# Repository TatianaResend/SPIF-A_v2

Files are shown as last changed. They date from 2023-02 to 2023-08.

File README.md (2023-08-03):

<!-- Improved compatibility of back to top link: See: https://github.com/othneildrew/Best-README-Template/pull/73 -->

<!--
*** Thanks for checking out the Best-README-Template. If you have a suggestion
*** that would make this better, please fork the repo and create a pull request
*** or simply open an issue with the tag "enhancement".
*** Don't forget to give the project a star!
*** Thanks again! Now go create something AMAZING! :D
-->

<!-- PROJECT SHIELDS -->
<!--
*** I'm using markdown "reference style" links for readability.
*** Reference links are enclosed in brackets [ ] instead of parentheses ( ).
*** See the bottom of this document for the declaration of the reference variables
*** for contributors-url, forks-url, etc. This is an optional, concise syntax you may use.
*** https://www.markdownguide.org/basic-syntax/#reference-style-links
-->
[][contributors-url]
[][forks-url]
[][stars-url]
[][issues-url]
[][license-url]

<!-- PROJECT LOGO -->
<br />
<div align="center">
  <a href="https://github.com/othneildrew/Best-README-Template">
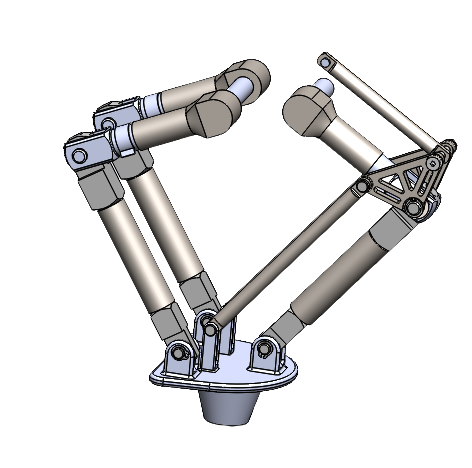
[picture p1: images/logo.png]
    
  </a>

  <h3 align="center">SPIF-A_v2</h3>

  <p align="center">
  It consists of the development of an incremental stamping machine   
  <br />
    <a href="https://github.com/TatianaResend/SPIFA-e-v2.0"><strong>Explore the docs »</strong></a>
    <br />
    <br />
    <a href="https://github.com/TatianaResend/SPIFA-e-v2.0/blob/main/README.md">View Demo</a>
    ·
    <a href="https://github.com/TatianaResend/SPIFA-e-v2.0/issues">Report Bug</a>
    ·
    <a href="https://github.com/TatianaResend/SPIFA-e-v2.0/issues">Request Feature</a>
  </p>
</div>

<!-- TABLE OF CONTENTS -->
<details>
  <summary>Table of Contents</summary>
  <ol>
    <li><a href="#about-the-project">About The Project</a></li>
    <li><a href="#machine-structure-design">Machine structure design</a>
      <ul>
        <li><a href="#base-requirements">Base requirements</a></li>
        <li><a href="#architecture">Architecture</a></li>
        <li><a href="#direct-and-indirect-kinematic-analysis">Direct and indirect kinematic analysis</a></li>
      </ul>
    </li>
    <li><a href="#mechanical-project">Mechanical project</a></li>
    <li><a href="#automation-project">Automation project</a></li>
    <li><a href="#contributing">Contributing</a></li>
    <li><a href="#license">License</a></li>
    <li><a href="#contact">Contact</a></li>
  </ol>
</details>

<!-- ABOUT THE PROJECT -->
# About The Project
The project serves as the focal point of the master's thesis in mechanical engineering. The primary goal of this project is to develop a compact incremental forming machine. The machine will be electric, ensuring a silent operation and compact size to facilitate coexistence with 3D printers. To effectively cover all aspects of machine construction, the project has been divided into three key areas: machine structure design, mechanical project, and automation project.

<!-- GETTING STARTED -->
# Machine structure design

## Base requirements:

|  |  |
| --- | --- |
| Number of axels | 3 |
| Working area  | 200 x 200 mm  |
| Vertical stroke  | 100 mm  |
| Sheet thickness  | 0,5 to 3 mm |
| Sheet material | aluminum |
| Conformation forces | 3 kN (vert.) 1 kN (hor.) |
| Motors | Nema 34 |

## Architecture:

The study of possible configurations is demonstrated in issues [#1](/../../issues/1) to [#4](/../../issues/4). After the analysis it is concluded that the best configuration is case 1.1.1..
To choose the best configuration, the lowest possible torque was taken into account.

- 2 arms in parallel (delta 2)
- Distance between motors: 50 mm
- L1 = 120;
- L2 = 150;
- y _ work area = -320 mm
- Maximum torque: 665 Nm 

## Direct and indirect kinematic analysis:
The direct and indirect kinematics are represented in the issue [#16](/../../issues/16) and in chapter 3.3 of the [thesis](https://github.com/TatianaResend/SPIF-A_v2/blob/main/Master's%20thesis.pdf) document.


# Mechanical project
Mechanical projects steps:
- Arm design
- Support system for the forming punch
- Selection and sizing of the motor-reducer set
- Selection and sizing of the linear motor-autorator set
- Structural configuration







### Simulation:
Two types of simulations were carried out using Solidworks: **with motion analysis** and **static** . Both analyzes are described in section 4.6.1 and 4.6.2, respectively, in the [thesis](https://github.com/TatianaResend/SPIF-A_v2/blob/main/Master's%20thesis.pdf) document. Some steps for carrying out the simulations are described in the issue [#5](/../../issues/5).

# Automation project
Automation projects steps:
- Wiring Diagram and Main Components
- Power Circuit
- Controller (**Controllino MEGA**)
- Drive (**CL86T Closed-loop Stepper Drive**)
- Security Elements
- Switchboard
- Motion Control: Implementation of Kinematics, Determination of the Number of Pulses, Incremental Positioning
- Graphic User Interface: Manual Mode, Automatic Mode, Information Page

<p align="center">
  
</p>

All steps of the automation project as well as its implementation are described in chapters 5 and 6.2 of the [thesis](https://github.com/TatianaResend/SPIF-A_v2/blob/main/Master's%20thesis.pdf) document. It is also possible to find some information in the issues [#15](/../../issues/15), [#17](/../../issues/17) - [#20](/../../issues/20), [#22](/../../issues/22) e [#23](/../../issues/23). The developed code can be found [here](https://github.com/TatianaResend/SPIF-A_v2/tree/main/CODE). The controller program was carried out in the **Arduino IDE** platform and the code for the GUI in **MATLAB.**

<!-- CONTRIBUTING -->
# Contributing

If you have a suggestion that would make this better, please fork the repo and create a pull request. You can also simply open an issue with the tag "enhancement".
Don't forget to give the project a star! Thanks again!

1. Fork the Project
2. Create your Feature Branch (`git checkout -b feature/AmazingFeature`)
3. Commit your Changes (`git commit -m 'Add some AmazingFeature'`)
4. Push to the Branch (`git push origin feature/AmazingFeature`)
5. Open a Pull Request

<p align="right">(<a href="#readme-top">back to top</a>)</p>

<!-- LICENSE -->
# License

Distributed under the GPL License. See `LICENSE.txt` for more information.

<p align="right">(<a href="#readme-top">back to top</a>)</p>

<!-- CONTACT -->
# Contact

Tatiana Resende - tatianaresende@ua.pt

Project Link: [SPIF-A_v2](https://github.com/TatianaResend/SPIFA-e-v2.0)

 <!-- <p align="right">(<a href="#readme-top">back to top</a>)</p> -->

<!-- ACKNOWLEDGEMENTS -->
### Acknowledgements
- Professor Ricardo Sousa - rsousa@ua.pt
- Professor Daniel Afonso - dan@ua.pt

<p align="right">(<a href="#readme-top">back to top</a>)</p>

<!-- MARKDOWN LINKS & IMAGES -->
<!-- https://www.markdownguide.org/basic-syntax/#reference-style-links -->
[contributors-shield]: https://img.shields.io/github/contributors/TatianaResend/SPIF-A_v2.svg?style=for-the-badge
[contributors-url]: https://github.com/TatianaResend/SPIF-A_v2/contributors
[forks-shield]: https://img.shields.io/github/forks/TatianaResend/SPIF-A_v2.svg?style=for-the-badge
[forks-url]: https://github.com/TatianaResend/SPIF-A_v2/network/members
[stars-shield]: https://img.shields.io/github/stars/TatianaResend/SPIF-A_v2.svg?style=for-the-badge
[stars-url]: https://github.com/TatianaResend/SPIF-A_v2/stargazers
[issues-shield]: https://img.shields.io/github/issues/TatianaResend/SPIF-A_v2.svg?style=for-the-badge
[issues-url]: https://github.com/TatianaResend/SPIF-A_v2/issues
[license-shield]: https://img.shields.io/github/license/TatianaResend/SPIF-A_v2.svg?style=for-the-badge
[license-url]: https://github.com/TatianaResend/SPIF-A_v2/blob/master/LICENSE.txt

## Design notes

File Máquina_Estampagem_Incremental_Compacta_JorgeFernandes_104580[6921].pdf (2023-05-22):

# RELATÓRIO

# Projeto e controlo de uma máquina de estampagem incremental compacta

### Jorge Fernandes, nº 104580

Curso Mestrado em Engenharia e Automação Industrial Disciplina Projeto em Engenharia de Automação

Ano letivo 2020/2021

Data | 16/07/2021
Orientador Professor Doutor Daniel Gil Afonso

Resumo Projeto do quadro elétrico, seleção de motores e programação da cinemática de uma máquina compacta para estampagem incremental baseada num braço RR plano.

Índice remissivo

Índice de figuras

### 1. Introdução

A utilização de máquinas controlados por comandos numéricos tem vindo a aumentar nas últimas décadas. São exemplos disso, o uso de CNCs, máquinas de corte a laser, impressoras 3D, braços robotizados, etc. Todos estes equipamentos trazem benefícios para a indústria em geral, reduzindo tempos de fabrico de componentes e aumentando a repetibilidade.
Por norma, o seu acionamento é feito por meio de um código, interpretado pela máquina de forma sequencial, contendo um conjunto de posições e/ou ações a ser tomadas. Este código, designado de código máquina ou g-code, é interpretado por um controlador responsável por acionar os componentes da máquina, como por exemplo motores, termístores, fusos, entre outros.

Neste projeto pretende-se selecionar um conjunto de componentes para controlo de uma máquina de estampagem incremental compacta baseada num braço robótico RR plano. Esta máquina tem um total de 3 eixos, X, Y, Z e será controlada por um controlador a selecionar. O controlador será responsável pela cinemática da máquina, para que se consiga o correto posicionamento da ferramenta de estampagem, um punção, nas múltiplas posições desejados de modo a conformar a chapa com a forma pretendida.
No decorrer deste projeto são selecionados: motores, drivers e todos os componentes elétricos de funcionamento e segurança necessário para o quadro elétrico. É determinada a cinemática da máquina e implementado o código para interpretação de comandos numéricos vindos do computador por porta de comunicação. Por último é desenvolvido uma interface para computador, de modo que o utilizador possa controlar a máquina de forma prática.

### 1.1 Estampagem incremental

O processo de estampagem incremental consiste numa tecnologia utilizada para conformar chapas de metal utilizando deformações incrementais sequenciais. É utilizada uma ferramenta de ponta arredondada, acoplada a uma CNC ou braço robótico, que deforma a chapa com o contorno da peça pretendida.
O percurso de uma peça fabricada por estampagem incremental começa pelo desenhado num software de CAD que é depois transferido para uma CNC, com o correto prato e sistema de grampos ou gabarito. Posiciona-se a chapa de metal na posição desejada, alinhada com a ferramenta de deformação e dá-se início ao processo. Finalizada a deformação, a peça está pronta a utilizar, não necessitando de nenhum processo adicional.
As principais aplicações de peças conformadas por estampagem incremental são protótipos, aplicações na medicina, aplicações aeronáuticas e automotivas sendo as suas vantagens:
- Facilidade na prototipagem rápida;
- Forças de conformação baixas, devido à natureza do processo incremental;
- É facilmente adaptado a qualquer tipo de CNC;
- Peças finais são produzidas diretamente dos ficheiros CAD;
- Não necessita de matrizes adicionais para a conformação;
- As dimensões das peças só são limitadas pelas dimensões da máquina;
- Excelente acabamento superficial.
Por outro lado, as desvantagens deste processo são:
- Elevados tempos de conformação quando comparado com outros processos de estampagem;
- Apresenta menor precisão dimensional especialmente em zonas com ângulos acentuados;
- Dificuldades na obtenção de ângulos retos;
- Pode ocorrer retorno do material (springback) após a conformação.
A Figura 1 ilustra alguns exemplos de estampagem incremental:

Figura 1 - Estampagem incremental

### 1.2 Máquina de estampagem incremental compacta

O projeto de construção de uma máquina de estampagem incremental compacta parte da necessidade de utilização de peças estampadas para protótipos. O acesso a uma máquina deste tipo, em conjunto com o uso de fresadoras ou impressoras 3D facilita a prototipagem rápida para testes ou ensaios.
Neste projeto é abordado somente as componentes elétricas e de comando da máquina, contudo para a programação da cinemática e para a seleção dos motores são tidos em conta a forma, as forças e os momentos da máquina durante o processo de estampagem. Será utilizado para controlo da ferramenta, nas coordenadas Y e Z, um braço robótico RR plano e para controlo do eixo X, onde fica o prato de suporte da chapa, será utilizado dois fusos.

As dimensões definidas para a máquina são:
- Braço de 120 mm posicionado a uma altura de 200 mm da base;
- Antebraço de 200 mm;
- Prato quadrado de lado 200 mm.
O eixo de coordenados encontra-se no centro da máquina. [Figura 2]

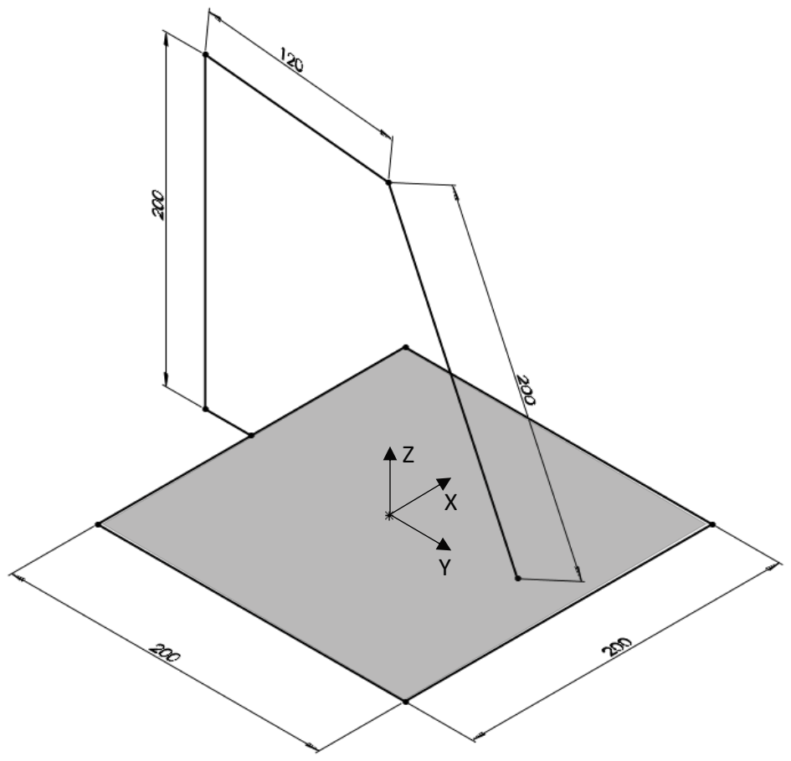
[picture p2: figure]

Estrutura da máquina, forças, velocidades, binários

Figura 2 - Máquina de estampagem compacta (Unifilar - vista isométrica)

Os 4 motores a selecionar MZ, MY, MX1 e MX2 serão posicionadas como na Figura
3. As forças máximas estimadas para a estampagem de chapa de alumínio são de: 3 kN no eixo vertical Z e 1 kN nos eixos horizontais Y e X. Os binários TZ, TY e TX esperados são de:

TZ = 660 Nm
TY = 400 Nm
TX = 32 Nm

Nas ligações aos 4 motores está previsto o uso de uma caixa redutora planetária com uma relação de transmissão de 100:1. Deste modo o binário máximo esperado no motor será 100 vezes menor do que o sentido nas ligações.
Apesar dos binários não serem iguais nos 3 eixos, serão selecionados motores semelhantes que satisfaçam os requisitos para o eixo Z, com um binário máximo de 660 Nm.
Posto isto, é esperado que os motores selecionados tenham um binário nominal de 6.6 Nm à velocidade máxima de funcionamento.

Figura 3 - Forças nos eixos Z, Y e X (Unifilar - vista lateral)

### 2. Seleção de motores

Os motores pretendidos para a aplicação devem garantir a completa conformação da peça sem que ocorrência de perca de passos. Ou seja, na presença de um aumento de binário, o motor deve garantir que finaliza todas as instruções enviadas pelo controlador. A maneira de conseguir este pressuposto é utilizando motores em malha fechada. Este tipo de motores possuem acoplado ao seu veio um componentes que vai enviar um sinal de resposta para o controlador, correspondente ao deslocamento real efetuado pelo veio, denominado de encoder. Assim sempre que o controlador enviar um determinado deslocamento para o motor, o encoder vai responder ao controlador com a quantidade de deslocamento real efetuado pelo veio do motor e o controlador vai saber sempre se o motor se encontra na posição correta. No caso de falha, o controlador deve tomar uma ação. A Figura 4 ilustra o funcionamento de um motor em malha fechada.

Dentro do mercado existem diferentes ofertas no que toca a motores de malha fechada sendo os ponderados para a aplicação: servo motores, motores sem escovas de corrente contínua (BLDC – brushless direct current) e motores de passo.

### 2.1 Motores sem escova de corrente contínua (BLDC)

Foi ponderado para os motores sem escovas de corrente contínua (BLDC) o uso do motor ODrive. Este motor possui o seu próprio controlador, que é programado em linguagem python. O controlador ODrive possui todas as conexões para ligar os 3 fios de dois motores BLDC (o controlador contém o ESC integrado – Electronic Speed Control), ligações para um encoder de cada motor, ligações para alimentação, ligações para a resistência de travagem e ligação USB [Figura 5].

Figura 5 - Ligações ODrive

Este controlador não obriga a utilizar motores da sua marca, mas só trabalha com motores BLDC. Os motores compatíveis com o ODrive têm binários de trabalho na média dos 4 Nm e a característica de apresentarem um binário maior para elevadas rotações.
Nesta aplicação, as velocidades são reduzidas, mesmo com a caixa redutora utilizada, e os binários desejados para os motores são da ordem dos 7 Nm, assim concluiu-se que este tipo de motores não seria o mais apropriado.
Contudo é importante referir que o controlador ODrive apresenta grandes potencialidades a um preço reduzido quando comparado com outros produtos do género. É um controlador ideal para aplicações como CNCs de gravação (engraving machines, cartesian plotter), braços robóticos de bancada, e todo o tipo de aplicações que trabalhem com baixos/médios binários e velocidades elevadas que necessitem de um elevado controlo de precisão.

### 2.2 Servo motores

Os servo motores são os mais utilizados a nível industrial. Estes apresentam uma elevada gama de binários e velocidades, compatíveis com todo o tipo de aplicações.
Cada motor possui o seu driver associado, sendo o driver o componente responsável por controlar a tensão e corrente que chegam ao motor. Este driver pode ser comandado por um controlador separado, ou em alguns casos pode funcionar sozinho, necessitando de uma programação dedicada.
No que toca a servo motores, a oferta no mercado é enorme, mas os preços são bastante mais elevados quando comparados com o ODrive. Foram consultados os modelos:
- Yaskawa Sigma 5;
- Mitsubishi MELSERVO;
- Oriental Motors BMU Series;
- Delta Servo System ECMA.
Qualquer uma destas marcas apresentava soluções com binário suficiente para a aplicação, contudo nenhuma se encontrava dentro do orçamento estipulado inicialmente. Concluiu-se que os servo motores, apesar de satisfazerem perfeitamente as exigências da aplicação, os preços praticados não se enquadram neste projeto.

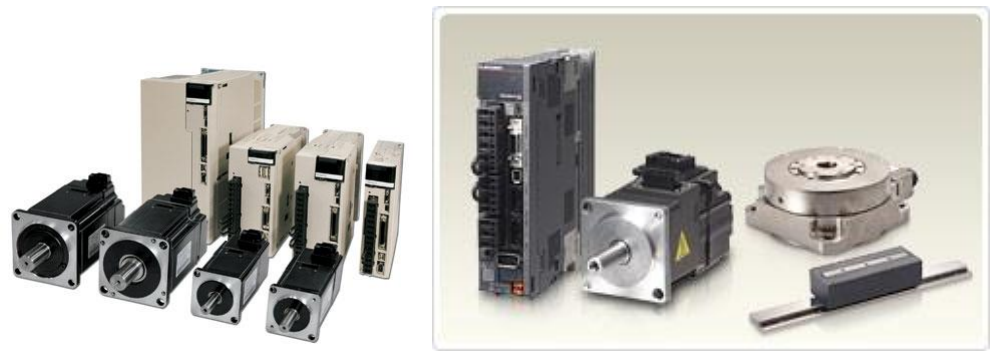
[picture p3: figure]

Figura 6 - Exemplos de servo motores

### 2.3 Motores de passo (solução proposta)

Como referido anteriormente, a máquina vai trabalhar a baixas velocidades e com elevados binários. Os motores de passo, em semelhança com os servo motores, são ligados a um driver, responsável pela gestão da tensão e da corrente para o motor. Estes motores apresentam a característica de um maior binário para baixa rotação, contudo a grande maioria trabalha em malha aberta, ou seja, não existe comunicação vinda do motor. Este funcionamento pode ser contornado com o uso de motores de eixo duplo, acoplando um encoder numa das extremidades do eixo.

No mercado já existem soluções deste género, onde os motores de passo são acoplados a um encoder, e a resposta do encoder é enviada para o controlador ou para o driver. Na grande maioria das aplicações profissionais, este sinal é na verdade enviado para o driver. Este tipo de drivers possui um circuito integrado que processa os sinais vindos do encoder. Deste modo reduz-se a quantidade de informação que o controlador necessita de processar, aumentado a sua performance.

Com isto, a procura dos motores indicados para a aplicação assenta em encontrar motores de passo, que funcionem em malha fechada e apresentem binário suficiente para satisfazer as forças e momentos estimados.
Foram contatados vários fornecedores para que se procedesse a uma comparação preço/qualidade onde se selecionaram 3 propostas:
Damen CNC [Figura 7]:
- 4 x Kit de motor + driver e cabos;
- Motor de passo NEMA 34 de 8 Nm com encoder;
- Driver HBS86 30-80 VDC, 8.2 A de corrente de pico;
- Cabo de ligação do encoder com 3 metros;
- Cada por 289.99€;
- 4 x fonte de alimentação de 48 VDC 400 W cada por 74.99€.
O fornecedor é sediado na Holanda, assim incluindo o valor de transporte e IVA o equipamento terá um custo total de 1808.85€.

Figura 7 - Encomanda Damen CNC

StepperOnline [Figura 8]:
- 3 x Kit de motor + driver e cabos;
- Motor de passo NEMA 34 de 12 Nm com encoder;
- Driver CL86T 24-80 VDC, 8.2 A de corrente de pico;
- Cada por 170.89€;
- 1 x Motor de passo NEMA 34 de 12 Nm com encoder e travão para o eixo Z por 174.56€;
- 1 x Driver CL86T 24-80 VDC, 8.2 A de corrente de pico por 52.30€;
- 4 x fonte de alimentação de 48 VDC 400 W por 25.38€;
- 1 x fonte de alimentação de 24 VDC 100 W por 10.15€.
A sede do fornecedor é na China, assim incluindo o valor de transporte e IVA o equipamento terá um custo total de 1509.97€. Nesta encomenda foi incluída uma fonte de alimentação de 24 VDC destinada ao controlador.

Figura 8 - Encomenda StepperOnline

Igus [Figura 9]:
- 3 x Motor de passo NEMA 34 de 5.9 Nm com encoder, cada por 635€;
- 1 x Motor de passo NEMA 34 de 5.9 Nm com encoder e travão para o eixo Z por 946.42€;
- 4 x Driver Drylin D1 12-48 VDC, 21 A de corrente de pico cada por 386.58€. Este driver funciona como controlador para 1 eixo com:

- 10 entradas digitais;
- 5 saídas digitais;
- 2 entradas analógicas de sinal ±10 VDC;
- Controlo por computador, tablet ou PLC;
- Comunicação por CANopen e/ou ModbusTCP; Este fornecedor faz o envio de Portugal, assim incluindo o valor de transporte e IVA o equipamento terá um custo total de 5481.40€. Nesta encomenda não são contempladas as fontes de alimentação.

Interessa referir que todos os fornecedores referidos têm certificação CE e respeitam a diretiva RoHS.

A Tabela 1 apresenta a comparação entre os fornecedores referidos:

Damen CNC | StepperOnline | Igus
Vantagens | Desvantagens | Vantagens | Desvantagens | Vantagens | Desvantagens
✓Dentro da União Europeia; | ✗ Não comercializa motor com travão; ✗ Binário máximo de 8 Nm; ✗ Preço total 1808.85€; | ✓ Binário de 12 Nm; ✓ Motor com travão; ✓ Preço total 1509.97€; | ✗ Encomenda vem da China; | ✓ Motor com travão; ✓ Comercializado em Portugal; ✓ Drivers de qualidade superior com funções de controlador; | ✗ Preço total 5481.40€; ✗ Binário máximo de 5.9 Nm; ✗ Encomenda não contempla as fontes de alimentação;

Tabela 1 - Comparação global entre fornecedores

As características comuns a todos não foram contempladas na tabela anterior. Com isto, a solução mais vantajosa é a proposta da StepperOnline, isto porque cumpre todos os requisitos e apresenta o custo mais baixo bem como o maior binário (holding torque).
Algumas características do motor selecionado encontram-se na Tabela 2:

Figura 9 - Encomenda Igus

Binário (holding torque) | 12 N.m
Bipolar | 2 enrolamentos, 4 fios
Corrente por fase | 6 A
Passo/pulso | 1.8º

Tabela 2 - NEMA 34

É esperado que os motores trabalhem a uma velocidade (feed rate) entre 500 e 1500 pulsos por segundo, o que dá um tempo entre pulsos de 2 milissegundos a 650 microssegundos, respetivamente. Uma velocidade aceitável para este tipo de motores.
O motor vai ser configurado para trabalhar a 400 pulsos por revolução, sendo este o menor valor aceite pelo driver selecionado. Este valor garante que se extrai o máximo de binário do driver.
Com esta configuração e com o feed rate mencionado é esperado que o motor trabalhe de 75 a 225 rpm. O binário mínimo esperado é de aproximadamente 7 Nm.
A Figura 10 apresenta a curva de binário do motor, disponibilizada pelo fornecedor.

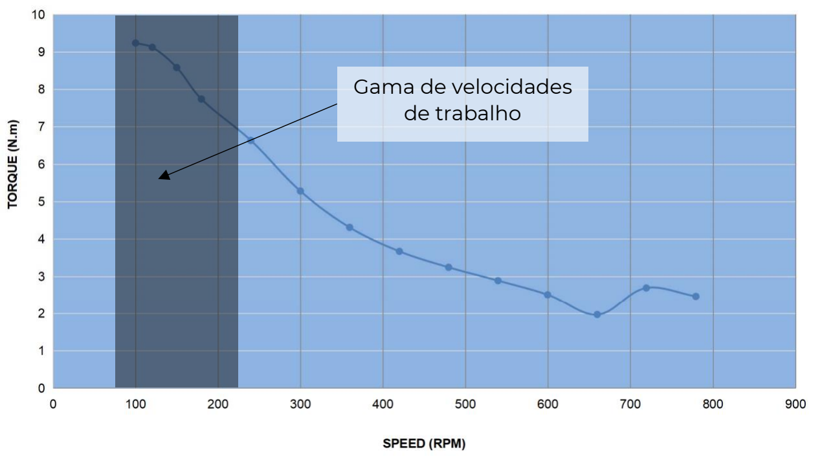
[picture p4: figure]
Gama de velocidades de trabalho

Figura 10 - Curva de binário do motor

A Figura 11 ilustra as ligações dos enrolamentos do motor ao driver com ficha GX16 fêmea:

Figura 11 - Conexões dos enrolamentos do motor

A Figura 12 ilustra as ligações do encoder ao driver da ficha DB15 macho:

Figura 12 - Conexões do encoder ao driver

A Figura 13 representa o desenho técnico do motor:

Figura 13 - Desenho técnico do motor

As características do driver são descritas na secção 3.3.

PIN 1 | A+
PIN2 | A-
PIN 3 | B+
PIN 4 | B-
PIN 1 | EA+
PIN 2 | VCC
PIN 3 | GND
PIN 11 | EB+
PIN 12 | EB-
PIN 13 | EA-

### 3. Esquema elétrico

Na elaboração do quadro elétrico são incluídos todos os componentes elétricos e eletrónicos responsáveis pelo funcionamento e controlo da máquina. São incluídos componentes de segurança de pessoas, bem como de proteção contra sobrecarga e curto-circuito.
O quadro é projetado para uma alimentação monofásica, de tensão alternada ~230V, 50 Hz, sendo esta a disponível nas tomadas em Portugal. A Figura 14 ilustra as interações entre os componentes.

Os componentes de potência, bem como os componentes de segurança, são selecionados após uma pesquisa de mercado, tendo em conta as suas características elétricas e a relação preço/qualidade. A seleção das fontes de alimentação é feita tendo em conta os requisitos dos motores. O controlador é escolhido com base no tipo de programação a implementar e no número e tipo de entradas e saídas necessárias.
O esquema elétrico completo com a designação de todos os componentes selecionados pode ser consultado no Anexo 1.

Figura 14 - Esquema de ligações entre componentes

### 3.1 Circuito de potência

A energia é fornecida ligando uma ficha de tomada monofásica a uma ficha do tipo IEC C14 presente na lateral do quadro. Por sua vez esta passa por um seccionador geral de 3 polos 20A, onde só são utilizados dois polos. Um para a linha e outro para o neutro. Em série encontra-se um disjuntor diferencial de 25A, com proteção de pessoas de 30mA.
É incluída uma tomada auxiliar e respetivo disjuntor dentro do quadro caso seja necessário ligar algum equipamento externo que necessite de alimentação monofásica AC.
São também alimentados a 230V um sinal luminoso verde que acederá indicando que o circuito se encontra com tenção e uma ventoinha para resfriamento dos componentes no interior do quadro. O sinal luminoso é montado na porta frontal e a ventoinha na lateral. Estes últimos componentes são ligados em série com um fusível de 250V, 2A para proteção contra curto-circuito.
A alimentação segue para um conjunto de fontes de alimentação. Cada fonte de alimentação encontra-se ligada em séria com um disjuntor de 1 polo ligado na linha. Cada fonte de alimentação foi escolhida para o componente que vai alimentar. Optou-se por utilizar diferentes fontes de alimentação, uma para cada componente, em vez de utilizar uma de maior dimensão que alimentasse todo o circuito DC. Esta opção foi tida em conta após diálogo com o fornecedor dos motores e com a análise dos preços praticados para fontes com tensões e correntes de grande dimensão. Ao utilizar diferentes fontes de alimentação é também esperado uma maior estabilidade da corrente para os drivers e um menor aquecimento no interior do quadro. Assim tem-se um total de 5 fontes de alimentação, sendo quatro delas de 400W com saída de 48V DC e uma de 60W com saída de 24V DC. As fontes de 48V alimentam os diferentes drivers e a fonte de 24V alimenta o controlador, os componentes de segurança, fins de curso e sensores de homing. Para as fontes de alimentação de 48V é incluindo um componente de sinalização luminoso ligado em paralelo com a saída da fonte, que permite uma rápida análise do funcionamento da mesma. Para a fonte de 24V este componente não é necessário pois a fonte já traz um sinalizador luminoso incorporado. A Figura 15 e Figura 16 ilustram o esquema elétrico descrito.

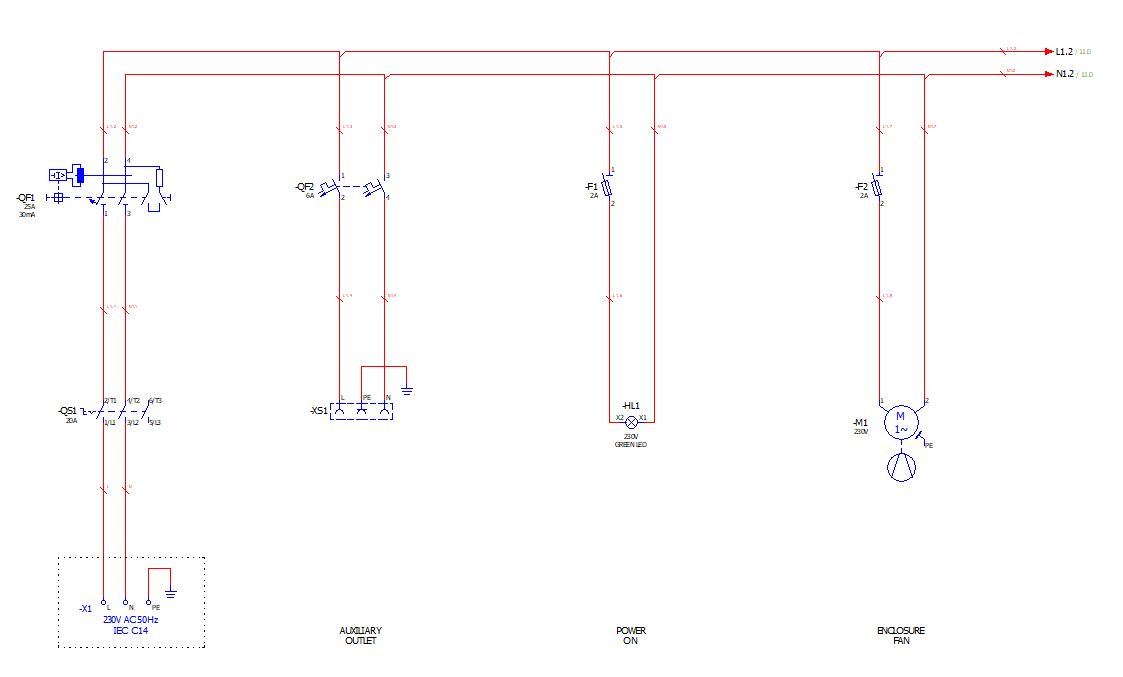
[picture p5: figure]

Figura 15 - Circuito de potência (parte 1)

Figura 16 - Circuito de potência (parte 2)

### 3.2 Controlador

Na seleção do controlador a selecionar foi feito um levantamento das entradas e saídas necessárias. Foi também escolhido uma linguagem de programação onde se consiga implementar as equações da cinemática da máquina.
A analise do mercado levou a considerar diferentes soluções, desde soluções mais industriais, utilizando o software Mach 3 ou Mach 4, até soluções mais baratas e open source como o GRBL e o Universal Gcode Sender.
Das soluções encontradas, as mais interessantes são:
- CPU5A4E 4-axis Ethernet Software, utilizando como software o Eding CNC, comercializado pela DemonCNC;
- Acorn Centroid, utilizando como software o Acorn CNC, comercializado pela Acorn;
- Ethernet SmoothStepper, utilizando como software o Mach 3;
- Masso G3, utilizando como software o Masso CNC, comercializado pela Masso;
- Machifit NVCM3, utilizando como software o Mach 4;
- Raspberry Pi 4, utilizando como software o LinuxCNC;
- BlackBox Motion Control System, utilizando o firmware o GRBL, comercializado pela OpenBluids.
Com a detalhada análise destas opções, percebeu-se que a escolha devia assentar naquela onde a implementação das equações da cinemática fosse possível. Assim, e devido ao teor académico deste projeto, dissidiu-se utilizar uma opção baseada em programação C/C++, e utilizar o Arduino IDE como software de programação. Neste ambiente de programação é então possível implementar o sistema de equações que satisfazem o funcionamento da máquina, bem como todas as entradas e saídas necessárias para o seu funcionamento.
Existem várias opções de microcontroladores no mercado compatíveis com o ambiente de programação Arduino. Dentro deles foi ponderado o microcontrolador da Espressif Systems ESP 32, o microcontrolador Teensy 4.1 da PJRC, mas optou-se por uma solução mais robusta, apta a trabalhar em ambientes mais agressivos, com semelhanças a um PLC.
Optou-se então por analisar soluções de PLCs compatíveis com linguagem Arduino, como é o caso do Controllino. Esta marca apresenta PLCs de diferentes dimensões, aptos para trabalhar em ambientes industriais e compatível com diferentes softwares de programação como Arduino IDE, Atmel Studio, PlatformIO entre outros. Algumas das suas características são:
- Entradas digitais compatíveis com 5V e 24V;
- Saídas digitais de 5V ou 24V;
- Saídas a relé que suportam até 250V, 16A;
- Modulo de relógio RTC integrado;
- Comunicação Serial UART RS232;
- Comunicação RS 485, I²C e SPI;
- Comunicação por USB e Ethernet.
Basta então determinar o número de entradas e saídas necessárias para que se possa escolher o modelo a selecionar da Controllino. A Tabela 3 contem o levantamento de entradas e saídas:

Sinal | Tipo | Quantidade
Botoeira de emergência | Entrada digital | 1
Sinal da barreira | Entrada digital | 1
Botoeira de rearm | Entrada digital | 1
Home switch | Entrada digital | 3
Alarme drivers | Entrada digital | 4
Fins de curso | Entrada digital | 3
Pulso drivers | Saída digital | 4
Direção drivers | Saída digital | 4
Enable drivers | Saída digital | 1

Tabela 3 - Lista de entradas e saídas

Verifica-se a necessidade de um total de 13 entradas digitais e 9 saídas digitais. Dos modelos apresentados pela Controllino, constata-se que o Controllino MAXI satisfaz os requisitos, contudo é selecionado o Controllino Mega para esta aplicação. O Controllino MEGA apresenta um maior número de entradas e saídas e a relação de preço quando comparado com o Controllino MAXI é vantajosa. As principais características do Controllino MEGA são:
- Microchip ATmega 2560;
- 256 kB de memória flash;
- 8 kB de SRAM;
- 4 kB de EEPROM
- 16 MHz de clock rate;
- 21 entradas digitais;
- 24 saídas digitais;
- 16 saídas a relé;
- Alimentação de 12V ou 24V.

Este PLC é então incluído no quadro elétrico, montado em trilha DIN, lado a lado com os restantes componentes. A sua alimentação é proveniente da fonte de 24V mencionada anteriormente e as suas entradas e saídas são conectadas diretamente aos componentes ou passando por bornes se necessário. Da porta USB do controllino mega é ligada uma extensão USB macho-fêmea de modo a tornar esta ligação acessível do exterior, sem que haja a necessidade da abertura da porta do quadro. A ligação USB fêmea é montada na porta frontal do quadro elétrico. A Figura 17 é uma representação real do controlador proposto para a aplicação. O esquema completo das ligações pode ser encontrado no Anexo 1.

Figura 17 - Controllino Mega

### 3.3 Drivers

O driver é o componente responsável por movimentar o motor. Este recebe os sinais vindos do controlador, nomeadamente pulso e direção, e converte esses sinais para o motor. Cada pulso recebido pelo driver corresponde a um dado deslocamento angular por parte do motor e controlando a frequência de pulsos consegue-se controlar a velocidade do motor. O sinal da direção permite definir o sentido de rotação, consoante este sinal está ligado ou desligado.
Assim pode dizer-se que o driver faz a ligação entre o circuito de baixa tensão, vindo do controlador, e o circuito de alta tensão, vindo da fonte de alimentação e indo para o motor. É no driver que se define a quantidade de corrente que deve ir para o motor, de modo que este tenho binário suficiente e não sobreaqueça. É também o driver que controla o número de pulsos necessários para que o motor complete uma rotação completa. Este valor pode ir desde os 400 pulsos por revolução até aos 51200 pulsos por revolução. Com o aumento deste valor consegue-se aumentar consideravelmente a precisão no posicionamento, à custa de uma perca de binário por parte do motor.
Como referido anteriormente, os motores vão funcionar em malha fechada, e neste caso em concreto, o controlo dos sinais do encoder e feito pelo driver. Existem opções de motores em que os sinais do encoder vão direto para o controlador, mas aqui é o driver que é encarregue por processar estes sinais, libertando espaço de processamento no controlador. Esta capacidade do driver de gerenciar os sinais enviados pelo encoder, é possível devido à existência de um microcontrolador incorporado no driver com um firmware dedicado para este propósito. Este firmware tem em si um conjunto de parâmetros configuráveis, que podem ser acedidos conectando o driver ao computador. É necessário instalar um software dedicado no computador e ligar a porta RJ-45 do driver, utilizando um cabo para comunicação RS 232 específico. Neste software é possível configurar as características de controlo de malha fechada. Isto é feito utilizando um controlo PID tanto para o controlo da corrente como para o posicionamento exato do motor. Aqui pode-se ajustar os valores proporcional, integral e derivativo característicos deste tipo de controlo (PID). É ainda possível definir um conjunto de características como:
- Corrente consumida quando o motor está parado;
- O tipo de sinal das saídas do driver (high(1) ou low(0));
- Ação a tomar para o sinal da entrada enable(ENA) do drive.
Com o driver ligado ao computador pode testar-se as configurações diretamente no motor, sendo possível simular velocidade e posicionamento com rampas de aceleração e desaceleração.
O driver possui duas saídas que podem ser ligadas a entradas do controlador. Uma é responsável pelo sinal de alarme em caso de falha de sincronismo entre o driver e o motor e a outra é responsável por avisar o controlador que o motor está em movimento.
Para o motor selecionado é fornecido uma tensão de 48V DC, sendo a corrente consumida pelo motor de 6A. O driver que melhor se enquadra nestes parâmetros é o driver modelo CL86T do mesmo fornecedor dos motores. Este driver permite o funcionamento com uma tensão de 20V a 80V DC e fornece uma corrente de pico de 8,2A. Possui entrada compatível com o encoder do motor e possui todas as entradas e saídas mencionadas anteriormente. A

Figura 18 ilustra as ligações entre os componentes, disponibilizada pelo fornecedor. Percebe-se que as entradas e saídas são ativadas pelo uso de fotodíodos e fototransístores.

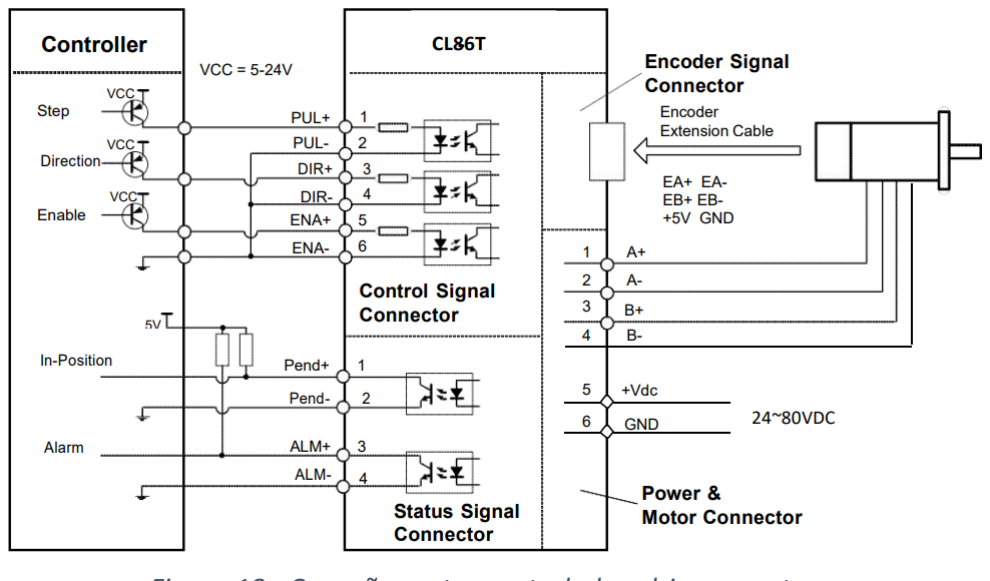
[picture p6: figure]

Figura 18 - Conexões entre controlador, driver e motor

Outras características do driver selecionado são:
- Frequência de pulse de entrada: 200kHz;
- Corrente média do sinal lógico: 7mA;
- Resistência do isolamento: 500MΩ;
- Peso: 580g.
No datasheet do driver é possível encontrar outras características como as suas dimensões e a configuração dos pinos da porta de comunicação RS 232.
São assim incluídos no quadro elétrico quatro drivers CL86T, cada um responsável pela movimentação de um motor. A Figura 19 é a representação real do driver proposto.

Figura 19 - Driver CL86T

### 3.4 Elementos de segurança

O processo de estampagem incremental é por norma efetuado a baixas velocidades de conformação, contudo, as forças utilizadas são de alguma grandeza. É assim importante ter em consideração o fator segurança, pois a utilização inadequada da máquina pode levar a lesões de alguma gravidade. O HRN (Hazard Rating Number) calcula o nível de risco que um equipamento ou máquina representa. É calculado tendo em conta 4 parâmetros tabelados que combinam a gravidade da lesão e a probabilidade de ocorrência. Tem-se:
- Possibilidade de ocorrência do perigo, designado por LO, aqui com o valor de 5 – Casual, pode ocorrer;
- Frequência de exposição ao perigo, designado de FE, aqui com o valor 5 – Constante;
- Perca máxima possível, designado de DPH, aqui com o valor 1 – Quebra ou lesão dos membros menores;
- Número de pessoas expostas, designado de NP, aqui com o valor 1 – Uma a duas pessoas;

HRN = LO ∗ FE ∗ DPH ∗ NP = 25

O valor de 25 determinado para o HRN indica um nível de baixo, mas relevante de risco de lesão, por essa razão é estipulada o uso de uma barreira imaterial na zona de acesso lateral da máquina. Esta barreira será acionada sempre que a máquina esteja ligada e algo aceda á zona de conformação. O seu restante perímetro pode ser envolto de uma parede de acrílico ou vedação de metal. Outra solução podia ser o uso de uma vedação no perímetro total, onde a zona lateral seria acedida por uma porta com interlock. Em ambos os casos, é gerado um sinal elétrico caso haja acesso à zona de conformação da máquina. Este sinal é usado para acionar o sistema de segurança para que tome uma ação imediata.
É aqui proposto o uso de uma barreira imaterial, com um comprimento de 150 mm, montada verticalmente e com uma tensão de alimentação de 24V. Esta barreira é composta por dois elementos, um recetor e um emissor e possui um sinal OSSD (Output Signal Switching Device) a ser ligado a um relé de segurança.
O relé de segurança deve conter um total de 2 entradas de acionamento vindas por parte da barreira imaterial e da botoeira de emergência e uma entrada de rearm feita pelo acionamento de uma botoeira. O relé vai então acionar a bobina auxiliar de um conjunto de 4 contatores e um e de um relé de 24V. Os contatores vão permitir a passagem de corrente dos drivers para os motores, ou seja, com a energia ligada os contatores encontram-se atracados e só vão abrir no caso de o relé de segurança ser acionado. O relé de 24V encontra-se da mesma forma acionado, e só abre no caso de falta de energia na sua bobina. Este relé tem como função acionar o travão do motor do eixo Z, que se encontra travado sempre que não está energizado.
Por outro lado, são utilizados dois sinais A1 e A2, levadas para entradas do controlador, acionadas pela botoeira de emergência e pela botoeira de rearm, respetivamente. Estas botoeiras podem estar fixas à porta do quadro elétrico, ou podem estar incorporados num comando móvel.
O sinal A0 pertence igualmente ao circuito de emergência, mas este é gerado pelo relé de segurança. São aqui usados sinais diferentes para que o controlador possa distinguir quando é pressionada a botoeira de emergência ou quando a barreira é atravessada. O esquema de ligações do relé de segurança escolhido encontram-se na Figura 20.

Figura 20 - Relé de segurança

A Figura 21 é uma representação real do relé de segurança proposto.

Figura 21 - Relé de segurança proposto

A Figura 22 representa o esquema de ligações da barreira imaterial.

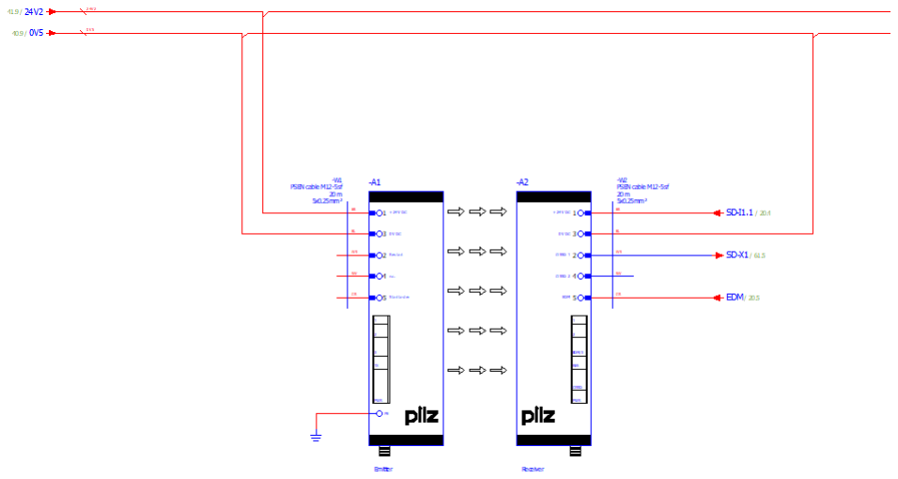
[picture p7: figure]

Figura 22 - Barreira imaterial

A Figura 23 é uma representação real da barreira imaterial proposta.

Figura 23 - Barreira imaterial proposta

### 3.5 Modelo 3D do quadro elétrico

A elaboração do modelo 3D do quadro elétrico teve em conta as dimensões reais de todos os componentes. Grande parte dos fornecedores disponibilizam os ficheiros CAD dos componentes selecionados e os restantes foram dimensionados com base nos desenhos técnicos dos mesmos. Utilizou-se o software SolidWorks para a montagem e o software KeyShot para a renderização.
A disposição dos componentes foi escolhida admitindo a entrada da energia no canto superior esquerdo do quadro e juntando os componentes do mesmo tipo por zonas.
- Zona 1: Entrada de potência e componentes de proteção;
- Zona 2: Drivers e contatores de acionamento dos motores;
- Zona 3: Bornes, relé de segurança, sinais luminosos e controlador;
- Zona 4: Fontes de alimentação.
O quadro está envolto por calha de plástico de modo a facilitar a passagem dos condutores de ligação dos componentes. Os componentes estão montados em calha DIN ou aparafusados diretamente na chapa de montagem.

Figura 24 - Quadro elétrico (vista frontal)

Figura 25 - Quadro elétrico

Na lateral do quadro são incorporadas 4 fichas GX16 de 4 pinos para ligação entre os drivers e os motores, 4 fichas DB15 de 3 linhas e uma ficha IEC C14.

Figura 26 - Quadro elétrico completo

### 4. Implementação da cinemática

Na implementação da cinemática para o controlo da máquina de estampagem incremental, é preconizado o controlo da extremidade da ferramenta de conformação. O objetivo é movimentar esta ferramenta para uma coordenada espacial (x, y, z) definida, controlando a aceleração e desaceleração do movimento. É admitido que a ferramenta pode deslocar-se 80 milímetros em Z, 220 milímetros em Y e 200 milímetros em X. O ponto 0,0,0 é definido no centro da máquina e admite-se um deslocamento negativo. Assim tem-se:
- Eixo X pode variar de [-100; +100];
- Eixo Y pode variar de [-110; +110];
- Eixo Z pode variar de [-40; +40].
Pretende-se que este deslocamento seja feito de forma síncrona, ou seja, todos os
motores | devem | acabar | o | seu | movimento | no | mesmo | instante,
independentemente do seu deslocamento. Pretende-se ainda que o movimento descreva uma linha reta no deslocamento entre pontos.

### 4.1 Determinação do número de pulsos

O controlo do eixo Z e Y é baseada num braço RR plano cujas equações da cinemática inversa para o cálculo dos ângulos para o caso específico são:

θ2 = −arccos

(120 − y)

2 + (200 − z)

2 − L1

2 − L2

2
2L1L2

;

θ1 = arctan [
(200 − z)(L1 + L2cosθ2

) − xL2sinθ2
(120 − y)(L1 + L2cosθ2

) − yL2sinθ2

];

As unidades θ1 e θ2 são calculadas em radianos, mas são facilmente convertidas para graus. Para os comprimentos do braço, L1 e L2, as dimensões adotadas são de 120 mm e 200 mm, respetivamente. A base do eixo Z é colocada a uma distância de 200 mm de altura, conforme referido na secção 1.2. Uma representação gráfica das dimensões do RR plano encontra-se na Figura 27.

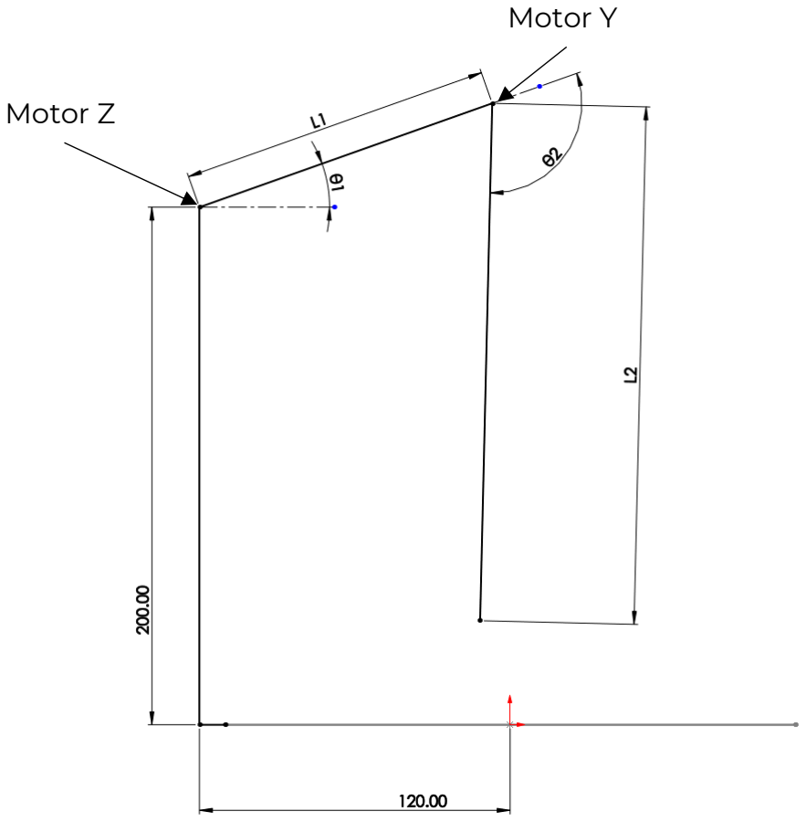
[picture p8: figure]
Motor Z; Motor Y

Figura 27 - Representação RR plano

Sabendo o valor dos ângulos é possível determinar o deslocamento angular que deve ser feito pelo motor para este se deslocar da posição atual para a posição desejada. Sabendo o número de pulsos para uma revolução pode calcular-se o número de pulsos necessários. Admite-se a utilização de uma caixa redutora entre a saída do motor e a ligação ao braço de 100:1, assim percebe-se que a rotação do motor deve ser 100 vezes maior que o deslocamento do braço. O número de pulsos para o motor Z e para o motor Y é calculado por:

nº de pulsos motor Z = θ1 [deg] ∗ redução ∗

pulsos/rev
360º ;

nº de pulsos motor Y = θ2 [deg] ∗ redução ∗

pulsos/rev
360º ;

O eixo X é controlado pela movimentação de dois fusos coordenados. É admito o uso de um fuso de passo 4 milímetros e é utilizado o mesmo sinal do controlador para ambus os drivers, ou seja, trata-se o eixo X como se fosse controlado por um único motor. A equação utilizada no cálculo do número de pulsos para o motor, admitindo também uma redução de 100:1 é:

nº de pulsos motor X = (xf − xi) ∗

pulsos/rev
passo

;

Com estas equações é possível determinar o número de pulsos que o controlador deve enviar para cada motor.

### 4.2 Controlo da aceleração e desaceleração

Para implementar uma aceleração no movimento dos motores de passo deve-se variar o intervalo de tempo entre cada pulso, partindo de um valor inicial prédeterminado, reduzindo este valor até um intervalo de tempo entre pulsos mínimo, sendo este a velocidade máxima do movimento. A partir deste momento, pretende-se que a velocidade seja constante até que entre no período de desaceleração parando na posição final. Neste período o intervalo de tempo entre pulsos aumenta até o valor inicial.
O cálculo do valor inicial, ou seja, o primeiro intervalo entre pulsos, pode ser estimado. Sabe-se que a velocidade, v, pode ser calculada em função da aceleração, α, e do tempo, t, por:

v = ∫ α dt = αt;

O deslocamento, s, é calculado por:

s = ∫ vt dt =

1
2

αt²
;

Por outro lado, o deslocamento de um motor de passo também é calculado em função do número de pulsos, n, e do ângulo/pulso, β, por:

s = nβ;

Assim igualando as duas expressões anteriores, pode determinar-se um tempo para uma determinada posição tem-se:

1
2

αt

2 = nβ <=> t = √
2nβ
α

A partir da expressão anterior é possível determinar uma expressão para o cálculo do intervalo entre dois pulsos consecutivos. Tem-se:

cntn = tn+1 − tn = √
2β
α

(√n + 1 − √n);

A partir daqui pode-se determinar uma expressão que permite calcular um valor para os intervalos entre pulsos. Estes valores começam num valor inicial e os restantes valores dependem do anterior. Tem-se:

cn =

1
tn

√
2β
α

(√n + 1 − √n);

Por fim o valor inicial, c0, é calculado por:

c0 =

1
tn

√
2β
α

;

E o valor de cn:

cn = c0(√n + 1 − √n);

O cálculo dos diferentes valores de cn, são feitos por parte do controlador, e de forma a reduzir espaço de computação no cálculo de duas raízes quadradas, é usado uma aproximação para este valor com menor complexidade matemática. Esta aproximação foi obtida usando uma serie de Taylor, aqui é somente apresentada a expressão final:

cn = cn−1 −

2cn−1
4n + 1

;

Esta expressão introduz um erro de 0,44 para n=1, mas por outro lado permite um cálculo mais rápido por parte do controlador. Uma maneira de compensar este erro consiste em multiplicar c0 por 0,676 (Atmel, 2006).

Com base na expressão anterior, é possível criar um código cíclico, onde é calculado um novo valor para cn partindo de um valor inicial c0. O limite definido para este valor consiste no intervalo de tempo mínimo entre pulsos. Estes valores são afixados num array que é inserido sequencialmente nos intervalos entre pulsos. Em forma crescente quando o motor está em aceleração, e em forma decrescente em desaceleração.

### 4.3 Posicionamento incremental

Recorrendo às equações da cinemática é possível determinar o movimento angular, e por sua vez o número de pulsos que o motor deve executar para posicionar a ferramenta nas coordenadas desejadas. Ainda assim, o movimento conjunto dos motores, leva a que a ferramenta não descreve um movimento retilíneo, mas sim descreva um arco.
A maneira de contornar este comportamento, consiste em movimentar a ferramenta entre posições sucessíveis, recalculando a nova posição com base na posição anterior, utilizando um valor incremental para o deslocamento, até que a ferramenta atinja a posição final. Para uma dada posição final Xf, Yf e Zf, partindo de uma posição inicial X0, Y0 e Z0, é possível calcular um vetor deslocamento no plano YZ:

vetor = √(∆Y)
2 + (∆Z)

2 = √(Yf − Y0)
2 + (Zf − Z0)

2;

Pode também calcular-se o ângulo do vetor deslocamento com a horizontal, δ por:

δ =
{

arctan

∆Z
∆Y

= arctan (
Zf − Z0
Yf − Y0

) , Yf > Y0

arctan

∆Z
∆Y

= arctan (
Zf − Z0
Yf − Y0

) + π, Yf ≤ Y0

Este valor depende se o braço se encontra em avanço ou recuo, assim depende da posição final Yf.
Encontra-se uma representação esquemática na Figura 28:

Figura 28 - Posicionamento incremental

(Y0, Z0)

Admitindo um valor para o incremento mínimo entre posições, ∆s, pode escreverse o seguinte sistema de equações para as posições dos eixos Y e Z:

{

∆Yi
∆Zi

= {

Y0 + i ∗ ∆s ∗ cos δ
Z0 + i ∗ ∆s ∗ sen δ

;

Os valores das sucessivas posições de ∆Yi e ∆Zi são afixados num array com um comprimento igual ao número total de incrementos, Ni

, dado em função do
tamanho do vetor deslocamento:

Ni =

vetor
∆s

;

O posicionamento do eixo X é independente dos restantes movimentos, contudo pretende-se que os movimentos sejam coordenados entre os 3 eixos. A abordagem para este eixo consiste em pegar no número de incrementos que os eixos Y e Z vão executar e achar um valor para o incremento de ∆X em função da posição final, Xf e da posição inicial, X0.

∆sx =

∆X
Ni

=

Xf − X0
Ni

;

O cálculo das sucessivas posições de ∆Xi é:

∆Xi = X0 + i ∗ ∆sx;

Do mesmo modo, o valor das sucessivas posições de ∆Xi é afixado num array com o comprimento de Ni

O fluxograma da Figura 29 representa as etapas de cálculo efetuadas pelo controlador no posicionamento da ferramenta:

A implementação da aceleração e desaceleração dos motores é feita em simultâneo com o incrementar de i. Contudo o comprimento do array contendo os valores dos intervalos entre pulsos referidos anteriormente é de Ni

/2. Deste
modo consegue-se garantir que o motor entra em desaceleração mesmo quando os movimentos são curtos, ou seja, mesmo que o motor não chegue a atingir a velocidade máxima i.e. mínimo intervalo entre pulsos.

Figura 29 - Fluxograma de posionamento incremental

### 4.4 Projeto experimental

Como referido na seleção do controlador, a programação utilizada é baseada em C++ e o software utilizado é o Arduino IDE. De modo a efetuar uma simulação do funcionamento da máquina de forma aproximada, é utilizado um Arduino MEGA para implementação e teste do código. Apesar de existirem bastantes diferenças no uso do Controllino MEGA em relação ao uso do Arduino Mega, nomeadamente na atribuição das saídas e entradas analógicas e digitais, a implementação das rotinas de posicionamento são iguais. Em conjunto, são também utilizados 3 motores de passo bipolares e 3 drivers, cada um representando um dos eixos X, Y e Z. Tanto os motores como os drivers são diferentes dos selecionados na secção 3, contudo o funcionamento é semelhante, ambus utilizam pinos de pulso e direção. A alimentação dos drivers é feita por parte de uma fonte de alimentação de 12V DC, já o Arduino é alimentado pela sua porta USB.
São utilizados dois NEMA 23 para os eixos Y e Z, e um NEMA 11 para o eixo X. A documentação dos componentes apresenta as seguintes características:
NEMA 23 | NEMA 11
Eixo Y e Z | Eixo X
1,85 Nm | 0,095 Nm
2,80 A/fase | 0,67 A/fase
1.8 º/pulso | 1.8 º/pulso

Tabela 4 - Características dos motores de passo

Em conjunto utilizam-se os drivers TB6600:

Tensão de alimentação | 9-42 V DC
Resolução | 200 a 6400 Pulsos/Revolução
Corrente de pico | 4 A
Frequência de pulso máxima | 20 kHz

Tabela 5 - Características driver TB6600

Em semelhança aos drivers propostos na secção 3.3, no corpo deles existem um conjunto de seletores que permitem fazer o ajuste de corrente e de pulsos por revolução. A sua parametrização é feita com a consulta das tabelas gravadas na lateral do driver, Figura 30, aqui para o motor NEMA 11. Apesar da corrente por fase do motor ser de 0.67 A, o driver é parametrizado para uma corrente de 0.5 A. Deste modo evita-se o sobreaquecimento do motor, contudo à custa de perda de binário. Para os restantes drivers é utilizado a mesma abordagem, ou seja, ambus os drivers são parametrizas para uma corrente de 2 A, apesar dos motores aceitarem 2.8 A. Para todos os drivers é utilizado uma resolução de 200 pulsos por revolução.

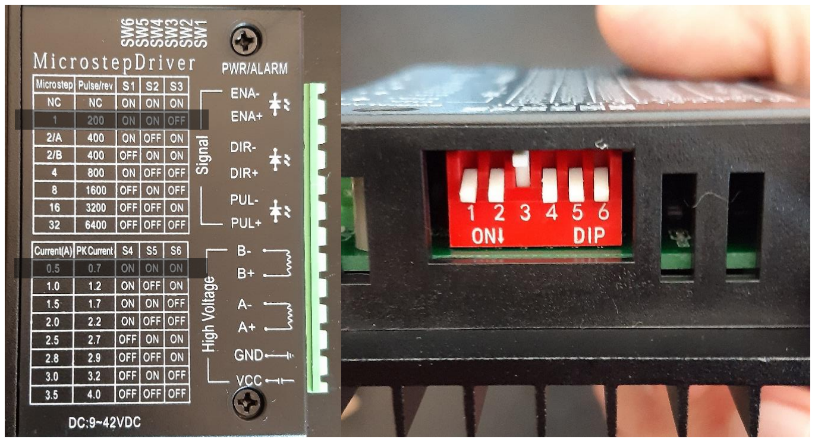
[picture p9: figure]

Figura 30 - Driver TB6600

A fonte de alimentação dos drivers e motores tem as seguintes características:

Modelo | S-201-12
Tensão de saída | 12 V DC
Corrente de saída | 16,5 A
Tensão de entrada | 115 V / 230 V AC com seletor
Corrente de entrada | 3.8 A / 2.0 A AC

Tabela 6 - Características da fonte de alimentação

São utilizados 3 fins de curso mecânicos, ligados ao Arduino Mega, que são usados como sensores limitadores de movimento, possibilitando a implementação de uma rotina de homing.
A montagem de todos os componentes numa banca de ensaio encontra-se na Figura 31 e 32. Todas as ligações são feitas com base na documentação dos componentes. As ligações ao Arduino dos sinais de pulso e direção utilizam os pinos digitais 2 a 7, o sinal enable para ativação dos drivers utiliza o pino 8 e os fins de curso utilizam os pinos digitais 18 a 20. Estes pinos têm a característica de funcionar como hardware interrupt, o que possibilita a criação de uma rotina de segurança de maior fiabilidade em caso de falha na movimentação dos motores. Estes sinais são do tipo normalmente fechado e utilizam uma resistência de pulldown de 3.3kΩ, assim o sinal no pino é sempre de aproximadamente 5V e vai a 0V quando o sensor (fim de curso) é ativado. Esta configuração permite detetar caso existam condutores desligados nos fins de curso.

Figura 31 - Montagem em bancada 1

Figura 32 - Montagem em bancada 2

### 4.5 Implementação do controlo numérico

Numa primeira fase, foi feito o controlo dos motores de passo de uma forma simples, gerando sinais de 0 V ou 5 V com um intervalo de tempo definido em microssegundos nos pinos do controlador ligados à entrada PUL+ do driver.
De seguida introduziu-se uma rotina de leitura de dados recebidos pela porta de comunicação RS 232 do Arduino. Esta porta vai ficar sempre à espera de mensagens, e vai executar um comando consoante a mensagem que receber. Começou-se por enviar pela porta de comunicação o número de pulsos pretendidos, e foram feitos alguns testes para determinar as velocidades máximas dos motores, ou seja, o mínimo tempo entre pulsos em microssegundos.
Por esta altura verificou-se que a abordagem que se estava a implementar, não garantia o funcionamento dos motores em simultâneo, nem a paragem de ambus numa determinada coordenada x, y, z. Verificou-se que o motor com menor distância atingia o ponto final mais rápido que os restantes motores, deste modo, devia definir-se as acelerações e velocidades dos motores para sincronizar este movimento.
Depois de investigação sobre o tópico, decidiu-se utilizar uma biblioteca para o Arduino IDE, a biblioteca AccelStepper. Esta biblioteca é bastante conhecida no que toca ao controlo de motores de passo e apresenta um vasto leque de classes para diferentes aplicações. Sobretudo, permite definir uma posição para os motores atribuindo um determinado número de pulsos. Com esta característica pode implementar-se uma rotina de homing para calibrar a posição dos motores e movimentar para as coordenadas desejadas a partir desta última. Tendo isto, todas as posições seguintes serão conhecidas de forma exata. Caso haja perda de passos, o encoder do motor vai detetar e avisar o driver que por sua vez informa o controlador.
Nesta biblioteca os diferentes motores são enumerados como objetos do tipo AccelStepper, atribuindo o tipo de motor (unipolar, bipolar, etc.), e os pinos de pulso e direção [Figura 33].

Figura 33 - Iniciação de objetos

Para o movimento conjunto dos motores recorre-se a classe MultiStepper. Esta classe aceita objetos do tipo MultiStepper, onde permite agrupar objetos do tipo AccelStepper com a função addStepper.
Na Figura 33 estão também definidos os pinos dos fins de curso que têm a característica de funcionarem como hardware interrupt. No Arduino mega os pinos com esta característica são os pinos 2, 3, 18, 19, 20 e 21. Aqui utilizam-se os pinos 18, 19 e 20. A implementação do hardware interrupt é feita na função setup(). Aqui é adicionada a função attachInterrupt() que tem como argumentos o pino, a função que deve ser chamada e o modo como a função é chamada, seja na descida (FALLING), subida (RISING) ou alteração (CHANGE) da extremidade de um sinal. Neste caso a função é chamada na descida.

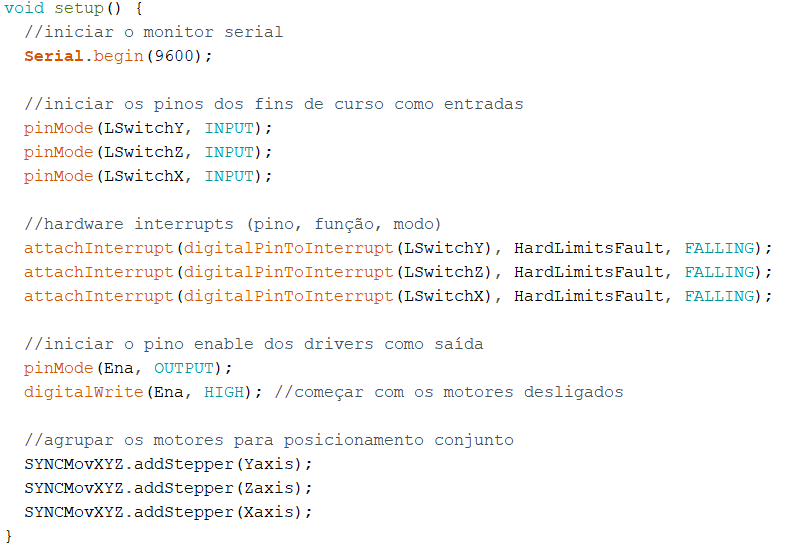
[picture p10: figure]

Figura 34 - Função setup

Após a função setup(), na função loop() apenas são chamadas a função de leitura de dados pela porta de comunicação, a função de posicionamento, função de calibração e função de sequência de movimentos. Estas função são dependentes de diferentes flags.

Figura 35 - Função loop

A função msgIn() tem como flag de entrada a chegada de bits à porta de comunicação. Os valores recebidos são concatenados numa string chamada msn_IN que é depois avaliada. Consoante o seu conteúdo o programa vai efetuar diferentes ações [Figura 36]:
- H – Executar rotina de calibração, homing;

- ENA – ligar os motores;
- DIS – desligar os motores;
- MOV – movimentos em sequência;
- SAV – guardar posições de sequência;
- ACC+ - ativar aceleração;
- ACC- - desativar aceleração.

Figura 36 - Leitura de mensagem recebida (parte 1)

Se a mensagem recebida for SET, os seus valores seguintes vão ser convertidos para variáveis do tipo integer e atribuídos aos valores da velocidade (vel), intervalo máximo entre pulsos (acc) e intervalo mínimo entre pulsos (MINdelay). Após a atribuição dos valores às variáveis, o programa responde de volta com os valores atuais das variáveis. Deste modo é possível garantir que os valores foram corretamente transmitidos. [Figura 37]

Figura 37 - Leitura de mensagem recebida (parte 2)

Por último, se não se cumprir nenhuma das condições anteriores, significa que os dados recebidos representam coordenadas de posicionamento. Estas valores são igualmente concatenados na string msn_IN, convertidos para integer e atribuídos a variáveis do tipo integer nomeadamente coordY, coordZ e coordX. É chamada a função CalcPos() e a flag DataReceived ganha o valor true.

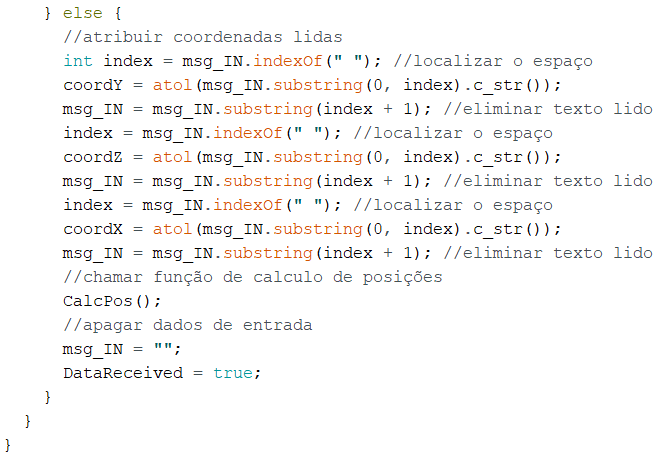
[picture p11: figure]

Figura 38 - Leitura de mensagem recebida (parte 3)

A função CalcPos() vai calcular o array de intervalos de tempo entre pulsos, responsável pela aceleração e desaceleração dos motores referido na secção 4.2., bem como o array de posições incrementais referido na secção 4.3. Ambus os arrays são calculados com um ciclo for de comprimento igual ao número total de incrementos. Os valores do vetor deslocamento YZ, do ângulo e do número de incrementos do eixo X são também calculados aqui.
Dentro do ciclo for responsável pelo cálculo do array de posições incrementais é chamada a função CinInv(). Esta função é responsável por calcular os valores dos ângulos referidos na secção 4.1 e respetivo número de pulsos para os eixos X, Y e Z.

Quando a flag DataReceived ganha o valor true, o código dentro da função IncPos() é executado e aqui começa-se por atribuir uma velocidade aos motores, depois é definida uma posição atual com base nos arrays calculados anteriormente.
A movimentação dos motores é feita neste momento, pelo recurso a um ciclo for, onde todos os valores de pulsos calculados são aqui enviados para os drivers. É também aqui que se implementa a aceleração e desaceleração. As funções que realmente movem os motores são as funções moveTo() e runSpeedToPosition() [Figura 39].

Figura 39 - Posicionamento incremental (parte 1)

O restante desta função consiste em atualizar as posições finais, desativar a flag e enviar os valores atuais das posições dos motores e o vetor pela porta de comunicação [Figura 40].

Figura 40 - Posicionamento incremental (parte 2)

Concluído estes passos os motores vão encontrar-se na posição final desejada. Para que o controlador saiba a posição dos motores quando a energia é ligada é necessário definir uma posição inicial. Isto é conseguido à custa dos fins de curso e de uma rotina de calibração. Esta rotina é executada quando a flag HomingRotine ganha o valor true, ou seja, quando se recebe a letra H na porta de comunicação.
A função de calibração, denominada Homing(), vai então movimentar os motores numa direção pré determinada até que os fins de curso sejam atingidos. Após isto, os motores deslocam-se na direção contrária até que deixem de tocar nos fins de curso. Cada motor faz este procedimento individualmente.
A Figura 41 demonstra como é implementado este processo para o eixo Z:

Figura 41 - Homing

Após a calibração de cada eixo o controlador envia uma mensagem pela porta de comunicação para confirmar o procedimento.
Quando todos os eixos estão calibrados o controlador atribui as coordenadas e respetivos pulsos às devidas variáveis:
- YHOME = −107;
- ZHOME = 68;
- XHOME = −100;
Por último o controlador indica que a calibração está concluída e atualiza as posições atuais pela porta de comunicação.

Como referido anteriormente os fins de curso encontram-se ligados a pinos com interrupt e a função que é chamada consiste numa função que imobiliza instantaneamente todos os motores enviando uma mensagem de falha [Figura 42]. Esta função é dependente de duas flags já referidas: HomingRotine e DataReceived. Assim é possível utilizar os fins de curso na rotina de calibração e estar à espera de mau funcionamento somente quando o código se encontra na rotina de posicionamento.

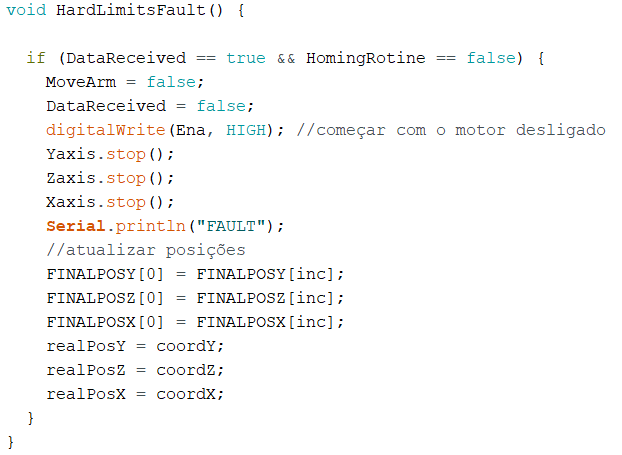
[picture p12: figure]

Figura 42 - Função de interrupt dos fins de curso

Esta função reinicia as flags e desativa os motores utilizando a função stop da biblioteca utilizada. De seguida atualiza as posições e obriga a uma rotina de calibração por parte do utilizador.

A última função a referir é a função Move(). Esta função é igualmente dependente de uma flag (MoveArm) e consiste numa função que executa um conjunto de movimentos predefinidos de forma sequencial, com ou sem aceleração. Os movimentos a executar são definidos pelo utilizador na planilha Sequential e atribuídos a variáveis do microcontrolador quando o utilizador pressiona o botão Save.

Todo este controlo de comunicação com o Arduino é feito por uma interface desenvolvida em VisualStudio para o propósito. Nesta interface o utilizador consegue facilmente controlar toda a máquina como:

- Configurar os parâmetros de comunicação [Figura 45];
- Configurar os valores de aceleração e velocidade máxima [Figura 45];
- Ligar ou desligar os motores [Figura 43];
- Efetuar a rotina de calibração [Figura 43];
- Posicionar a ferramenta numa coordenada X, Y e Z [Figura 43];
- Movimentação sequencial [Figura 44].

Figura 43 - Interface de controlo (1)

Figura 44 - Interface de controlo (2)

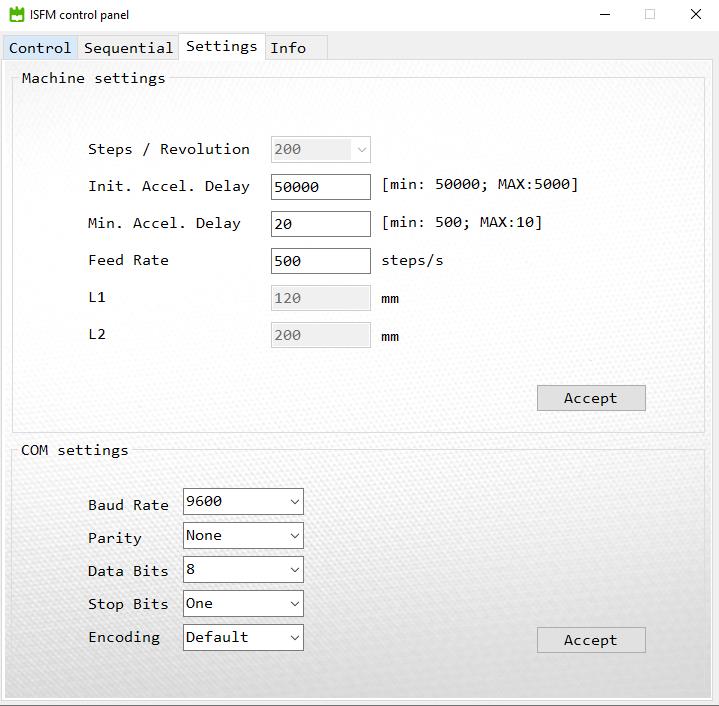
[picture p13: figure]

Figura 45 - Interface de controlo (3)

Com esta interface é possível configurar todos os parâmetros necessários para o controlo da máquina. Com o posicionamento sequencial pode efetuar-te até um total de 8 segmentos de reta utilizando o posicionamento incremental.
No botão acceleration ativa-se ou desativa-se a aceleração e desaceleração configurada na planilha settings.

Figura 46 - Interface de controlo (4)

A última planilha contém informações sobre como utilizar a interface. Todo o desenvolvimento e várias iterações deste projeto pode ser consultado em https://github.com/JorgeFernandes-Git/ISFM.

### 5. Conclusões

No decorrer do projeto foram cumpridos os vários objetivos propostos. Conseguiu-se o dimensionamento dos componentes elétricos de controlo e segurança, bem como dos motores. Devido ao aspeto académico deste projeto, deu-se enfase nos equipamentos elétricos de proteção e segurança como disjuntores, contatores e relé de segurança, contudo numa primeira fase de prototipagem, alguns componentes podem ser minimizados ou omitidos.

O controlo numérico implementado, apesar de conter muitas possibilidades de melhoramento, é capaz de posicionar a ferramenta da máquina numa coordenada definida, com controlo de velocidade, aceleração e desaceleração. Numa análise de comparação entre os valores matemáticos obtidos nas rotinas do controlador com valores obtidos numa folha de Excel, verificou pequenas diferenças nos valores dos cálculos dos ângulos da cinemática inversa e consequentemente nos valores dos pulsos a enviar para o motor. Inicialmente, foi verificado um erro médio de 12 pulsos para o motor Z e 19 pulsos para o motor Y, o que se traduzia num erro nos ângulos dos motores de 20º e 40º, respetivamente (motores de 1.8º / pulso). Após algumas melhorias, nomeadamente nas equações e no tipo de variáveis utilizadas (inteiros para flutuantes) conseguiu-se reduzir este erro para 2 pulsos em Z (4º) e 10 pulsos em Y (18º). É de notar que estes são os graus de desvio no motor; os graus na máquina serão 100 vezes menores devido ao uso da redução de 100:1 acoplado à saída dos motores. Assim, estes valores dos erros podem ser desprezados.
A remodelação do programa desenvolvido, no que toca às alterações nos tipos de variáveis e no aumento da resolução no número de incrementos entre posições, levou a um aumento drástico do uso da memoria dinâmica do controlador, o que pode afetar a sua performance, assim é importante melhorar o código com este aspeto em mente. Uma solução será utilizar equações de cinemática diferencial.

Relativamente aos motores, foi pedida uma pro-forma à StepperOnline do material referido na secção 2.3 para que se desse início à encomenda.

Por último interessa referir todo o conhecimento que este projeto trouce ao aluno no que toca ao controlo de máquinas por comandos numéricos. Todo o desenvolvimento da cinemática e do controlo de velocidade e aceleração dos motores introduziu um desafio na procura de diferentes soluções, pretendendo aplicar em conjunto os conhecimentos adquiridos na disciplina.

### 6. A implementar

Para projetos futuros era indispensável que o controlador executasse as múltiplas posições necessária para a conformação da chapa de forma sequencial. Uma maneira de isso ser possível seria o uso de um leitor de cartões SSD ligado ao controlador. Deste modo todas as posições seriam gravadas no cartão e lidas sequencialmente pelo controlador. Deste modo evita-se que o controlador esteja sempre ligado ao computador.

Outros pontos que são necessários implementar são a interpretação por parte do controlador dos sinais de alarme vindos dos drivers em caso da perca de passos no motor, bem como implementação do acionamento de rearme em caso de aperto da botoeira de emergência ou de quebra da barreira imaterial. Para este tipo de paragens e outras paragens não programadas, o controlador devia ter um espaço na sua memoria EEPROM definida a guardar a posição do código onde ficou, para que pudesse continuar da mesma posição caso fosse possível. A EEPROM também devia ficar responsável por guardar certas configurações na máquina quando esta fosse desligada, como por exemplo, a última posição dos eixos, as velocidades e acelerações.

Está também previsto o uso de fins de curso mecânicos como hard limits da máquina. Aqui foi implementado uma rotina de homing, que utilizam sensores de proximidade indutivos, mas era importante existirem sensores mecânicos logo a seguir para garantir uma maior segurança.

Os comandos numéricos enviados para o controlador foram desenvolvidos especificamente para esta aplicação e seria interessante serem melhorados de forma a aproximarem-se de comandos numéricos utilizados por outros equipamentos. Isto porque, a utilização de softwares como gerados de código máquina (g-code) permite passar peças modeladas em softwares de CAD para código máquina de forma rápida e simples. Para isso o controlador tem de estar apto a interpretar estes comandos.

### 7. Bibliografia

Single Point Incremental Forming and Multi-Stage Incremental Forming on Aluminium Alloy 1050, Premika Suriyaprakan, 2013

Atmel. (2006). AVR446: Linear speed control of stepper motor. http://www.atmel.com/images/doc8017.pdf

AccelStepper: AccelStepper Class Reference, from https://www.airspayce.com/mikem/arduino/AccelStepper/classAccelStepper. html#details

AccelStepper: MultiStepper Class Reference, from https://www.airspayce.com/mikem/arduino/AccelStepper/classMultiStepper. html#details

Apontamentos da disciplina de Projeto em Engenharia de Automação, 2021

### 8. Anexos

Anexo 1 – Quadro elétrico ISFM

E | E
F | F

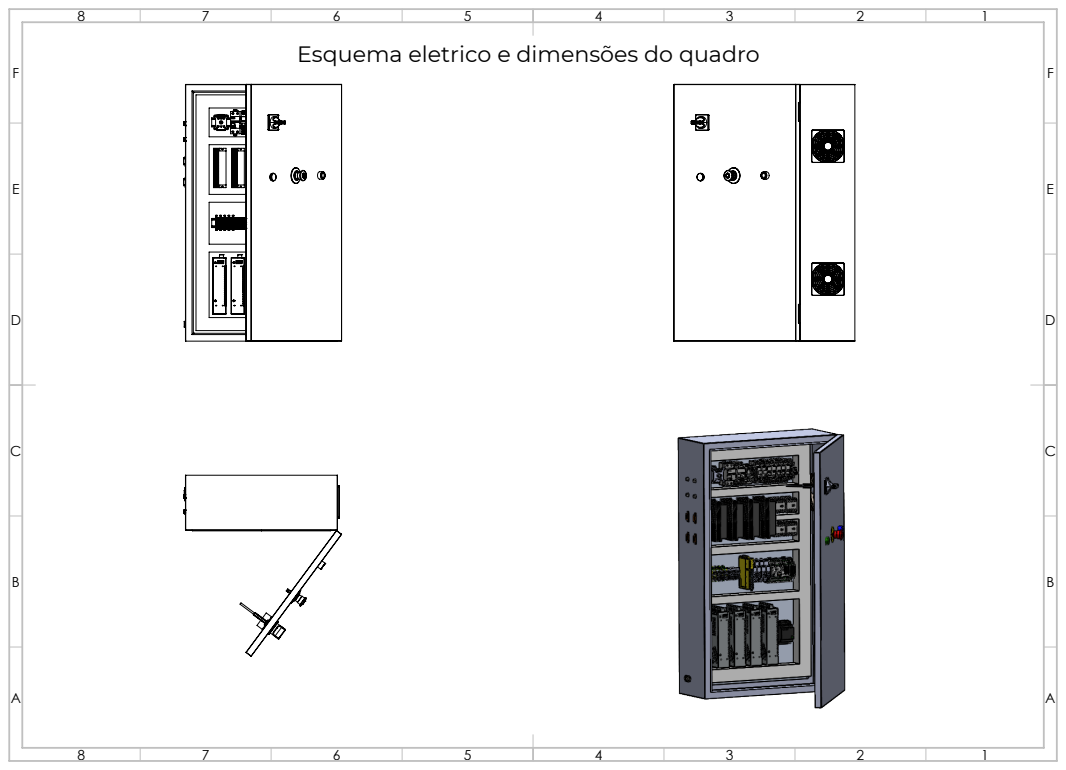
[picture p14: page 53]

Esquema eletrico e dimensões do quadro

5
A

10 | GX 16 4 PINOS X2 AXIS
11 | DB 15 LIGAÇÃO ENCODER Z AXIS
12 | DB 15 LIGAÇÃO ENCODER Y AXIS
13 | DB 15 LIGAÇÃO ENCODER X1 AXIS
14 | DB 15 LIGAÇÃO ENCODER X2 AXIS

1 | 2 | 3 | 4 | 5 | 6 | 7 | 8 | 9
| | | | | | | | 10

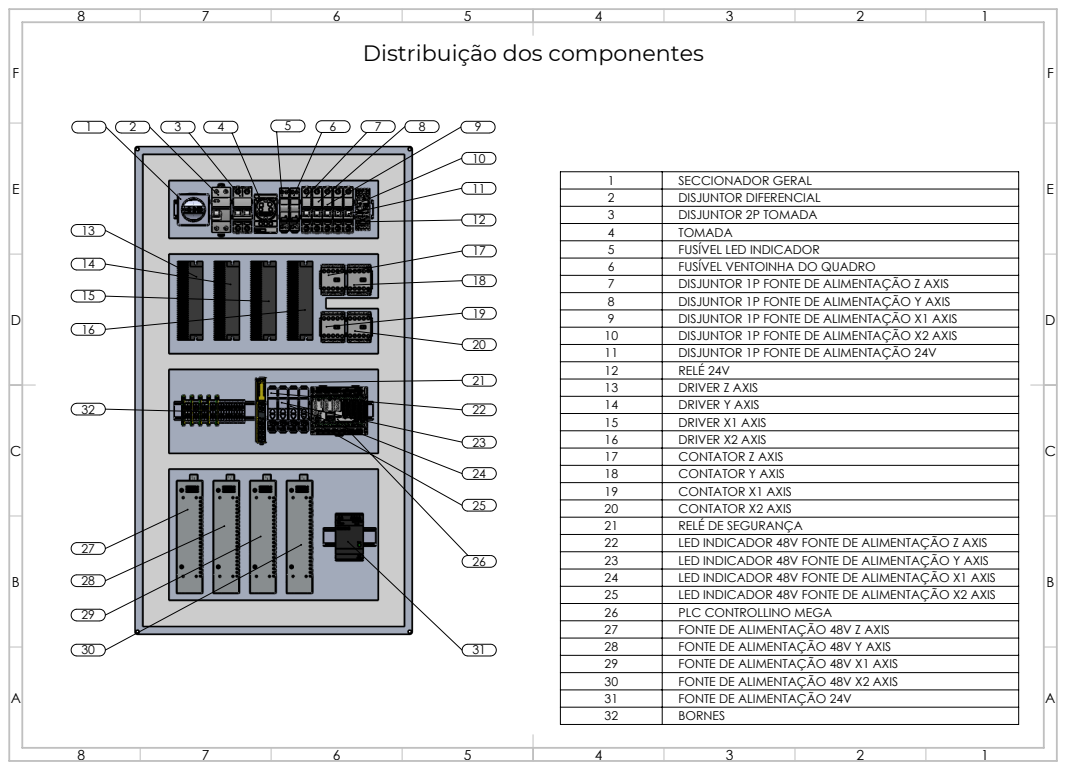
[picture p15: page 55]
RELÉ DE SEGURANÇA

Distribuição dos componentes

1 | SECCIONADOR GERAL
2 | DISJUNTOR DIFERENCIAL
3 | DISJUNTOR 2P TOMADA
4 | TOMADA
5 | FUSÍVEL LED INDICADOR
6 | FUSÍVEL VENTOINHA DO QUADRO
7 | DISJUNTOR 1P FONTE DE ALIMENTAÇÃO Z AXIS
8 | DISJUNTOR 1P FONTE DE ALIMENTAÇÃO Y AXIS
9 | DISJUNTOR 1P FONTE DE ALIMENTAÇÃO X1 AXIS
10 | DISJUNTOR 1P FONTE DE ALIMENTAÇÃO X2 AXIS
11 | DISJUNTOR 1P FONTE DE ALIMENTAÇÃO 24V
12 | RELÉ 24V
13 | DRIVER Z AXIS
14 | DRIVER Y AXIS
15 | DRIVER X1 AXIS
16 | DRIVER X2 AXIS
17 | CONTATOR Z AXIS
18 | CONTATOR Y AXIS
19 | CONTATOR X1 AXIS
20 | CONTATOR X2 AXIS

22 | LED INDICADOR 48V FONTE DE ALIMENTAÇÃO Z AXIS
23 | LED INDICADOR 48V FONTE DE ALIMENTAÇÃO Y AXIS
24 | LED INDICADOR 48V FONTE DE ALIMENTAÇÃO X1 AXIS
25 | LED INDICADOR 48V FONTE DE ALIMENTAÇÃO X2 AXIS
26 | PLC CONTROLLINO MEGA
27 | FONTE DE ALIMENTAÇÃO 48V Z AXIS
28 | FONTE DE ALIMENTAÇÃO 48V Y AXIS
29 | FONTE DE ALIMENTAÇÃO 48V X1 AXIS
30 | FONTE DE ALIMENTAÇÃO 48V X2 AXIS
31 | FONTE DE ALIMENTAÇÃO 24V
32 | BORNES

380.00
70

Dimensões (vista frontal)

1 | SECCIONADOR GERAL | -QS1 | Schneider | SE.VCCDN20
2 | DISJUNTOR DIFERENCIAL | -QF1 | Schneider | SE.A9R60225

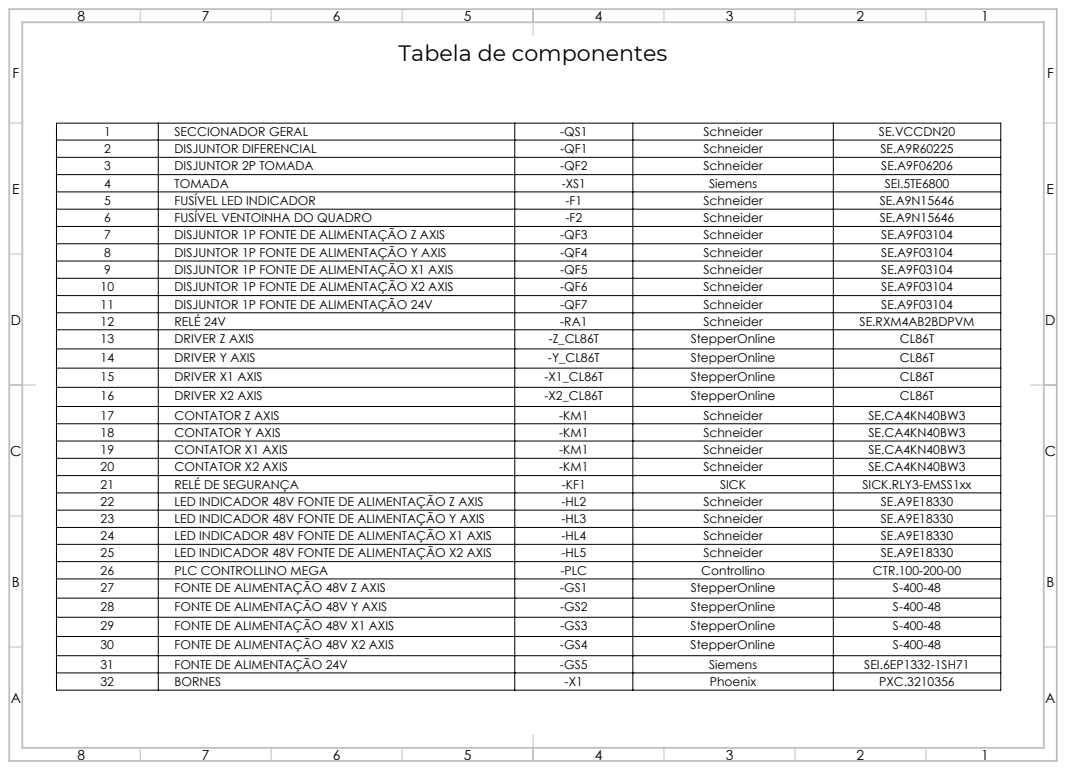
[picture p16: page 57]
DISJUNTOR 2P TOMADA; Schneider; TOMADA; Siemens; SEI.5TE6800; FUSÍVEL LED INDICADOR; FUSÍVEL VENTOINHA DO QUADRO; DISJUNTOR 1P FONTE DE ALIMENTAÇÃO Z AXIS; DISJUNTOR 1P FONTE DE ALIMENTAÇÃO Y AXIS; DISJUNTOR 1P FONTE DE ALIMENTAÇÃO X1 AXIS; DISJUNTOR 1P FONTE DE ALIMENTAÇÃO X2 AXIS; DISJUNTOR 1P FONTE DE ALIMENTAÇÃO 24V; RELÉ 24V; SE.RXM4AB2BDPVM; DRIVER Z AXIS; StepperOnline; DRIVER Y AXIS; DRIVER X1 AXIS; DRIVER X2 AXIS; CONTATOR Z AXIS; CONTATOR Y AXIS; CONTATOR X1 AXIS; CONTATOR X2 AXIS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

Tabela de componentes

## Esquema de Potência 1

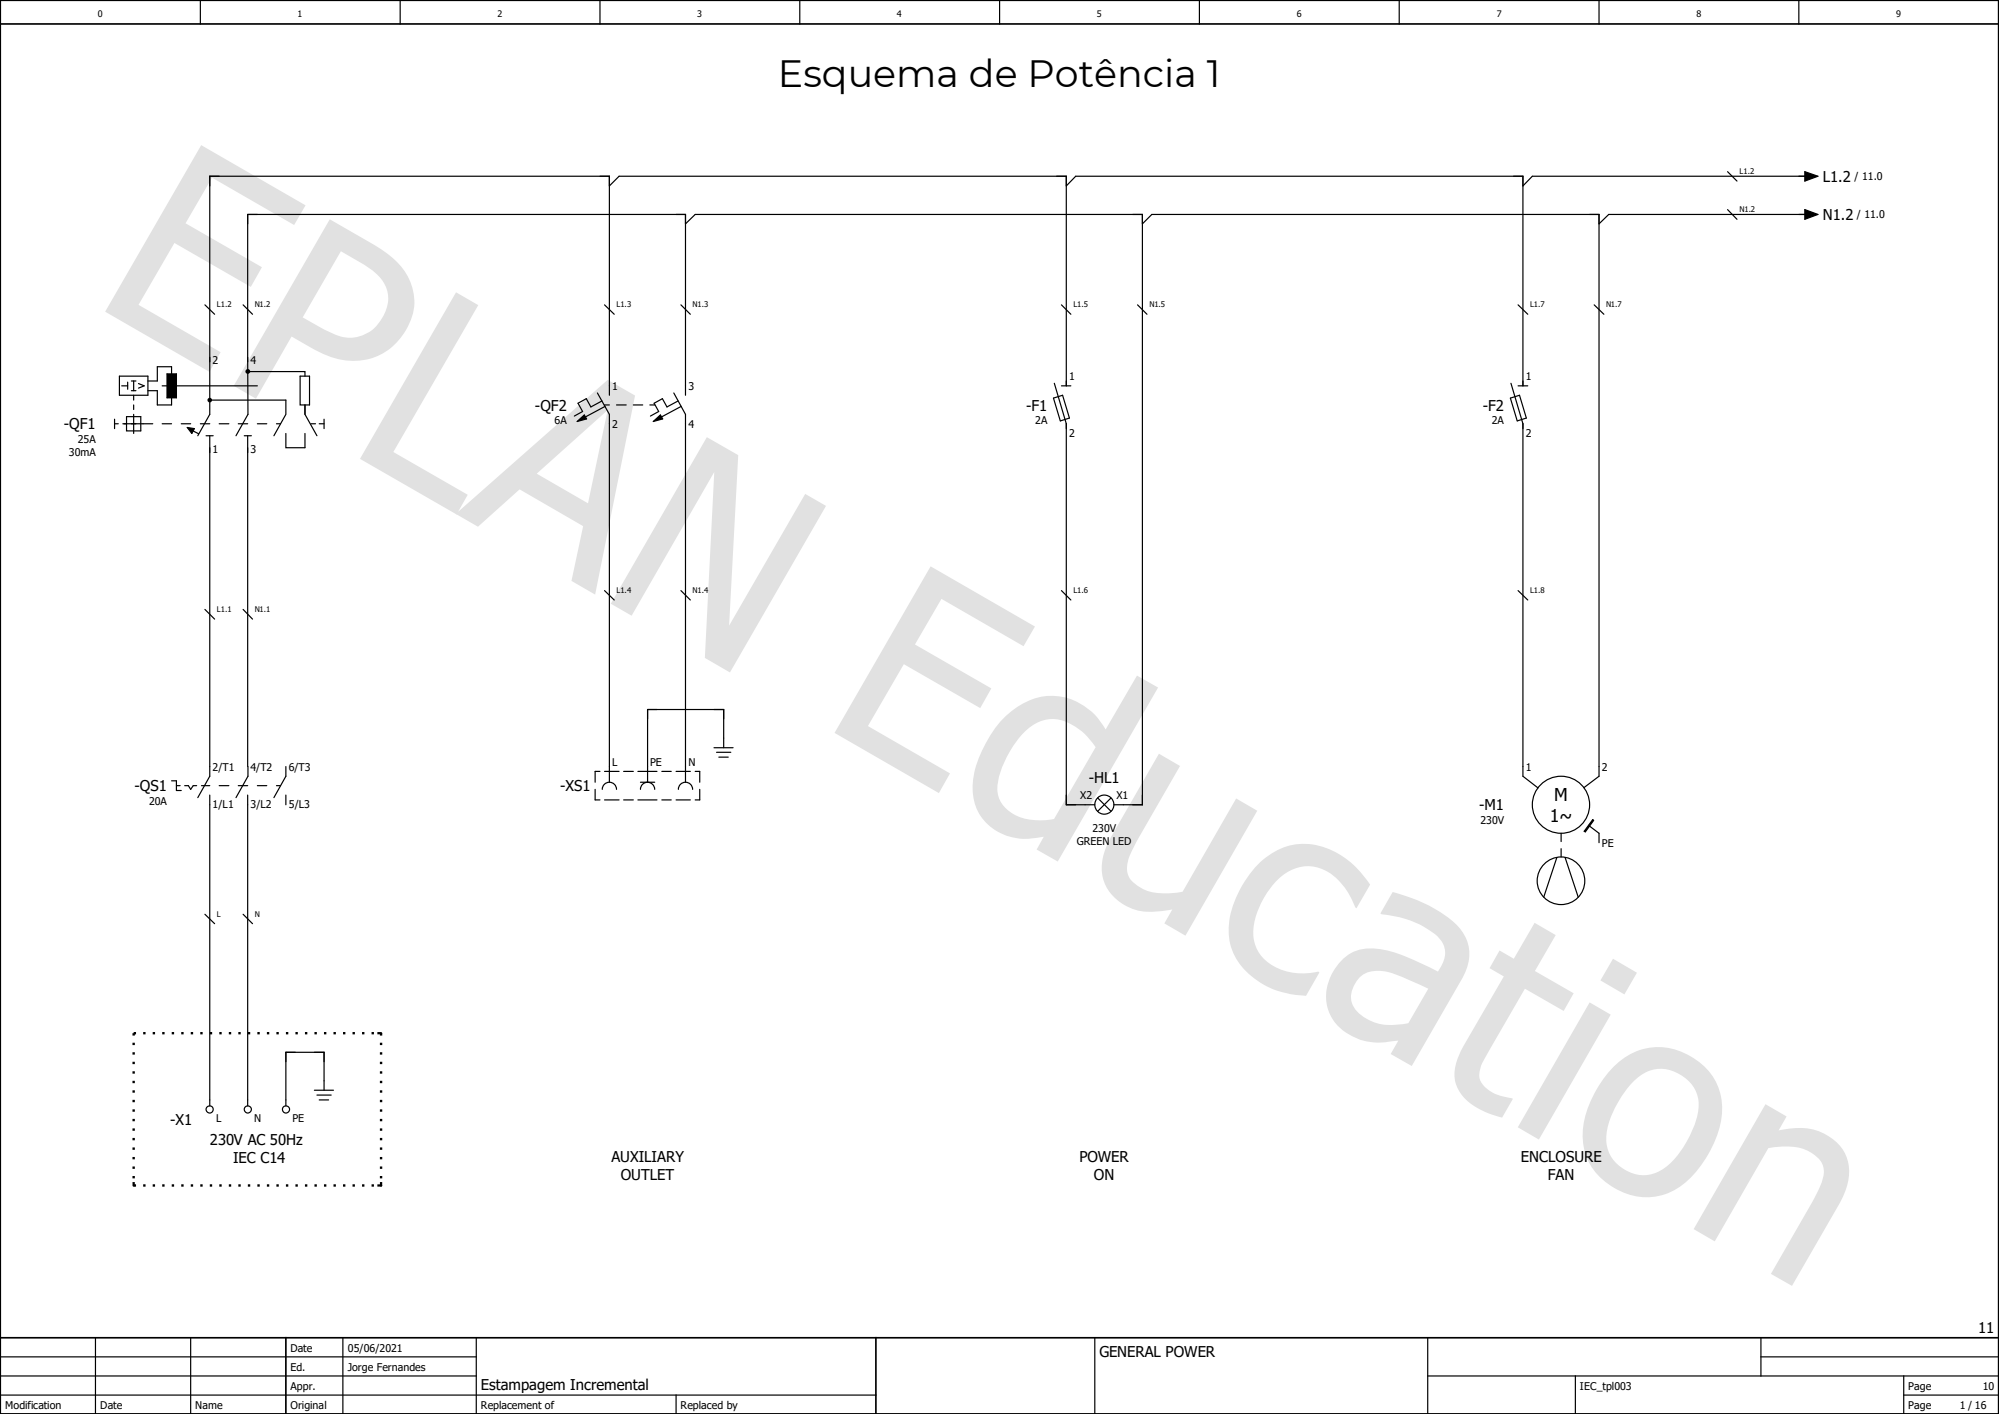
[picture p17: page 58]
IEC C14; AUXILIARY; OUTLET; ENCLOSURE FAN; POWER ON; NPE; 230V GREEN LED

Date | 05/06/2021 | Estampagem Incremental | | GENERAL POWER
Ed. | Jorge Fernandes
Appr. | | | | | IEC_tpl003 | Page 10

Modification | Date | Name | Original | | Replacement of | Replaced by | | | | Page 1 / 16

## Esquema de Potência 2

Date | 05/06/2021 | Estampagem Incremental | | GENERAL POWER
Ed. | Jorge Fernandes
Appr. | | | | | IEC_tpl003 | Page 11

Modification | Date | Name | Original | | Replacement of | Replaced by | | | | Page 2 / 16

## Caixa de comando

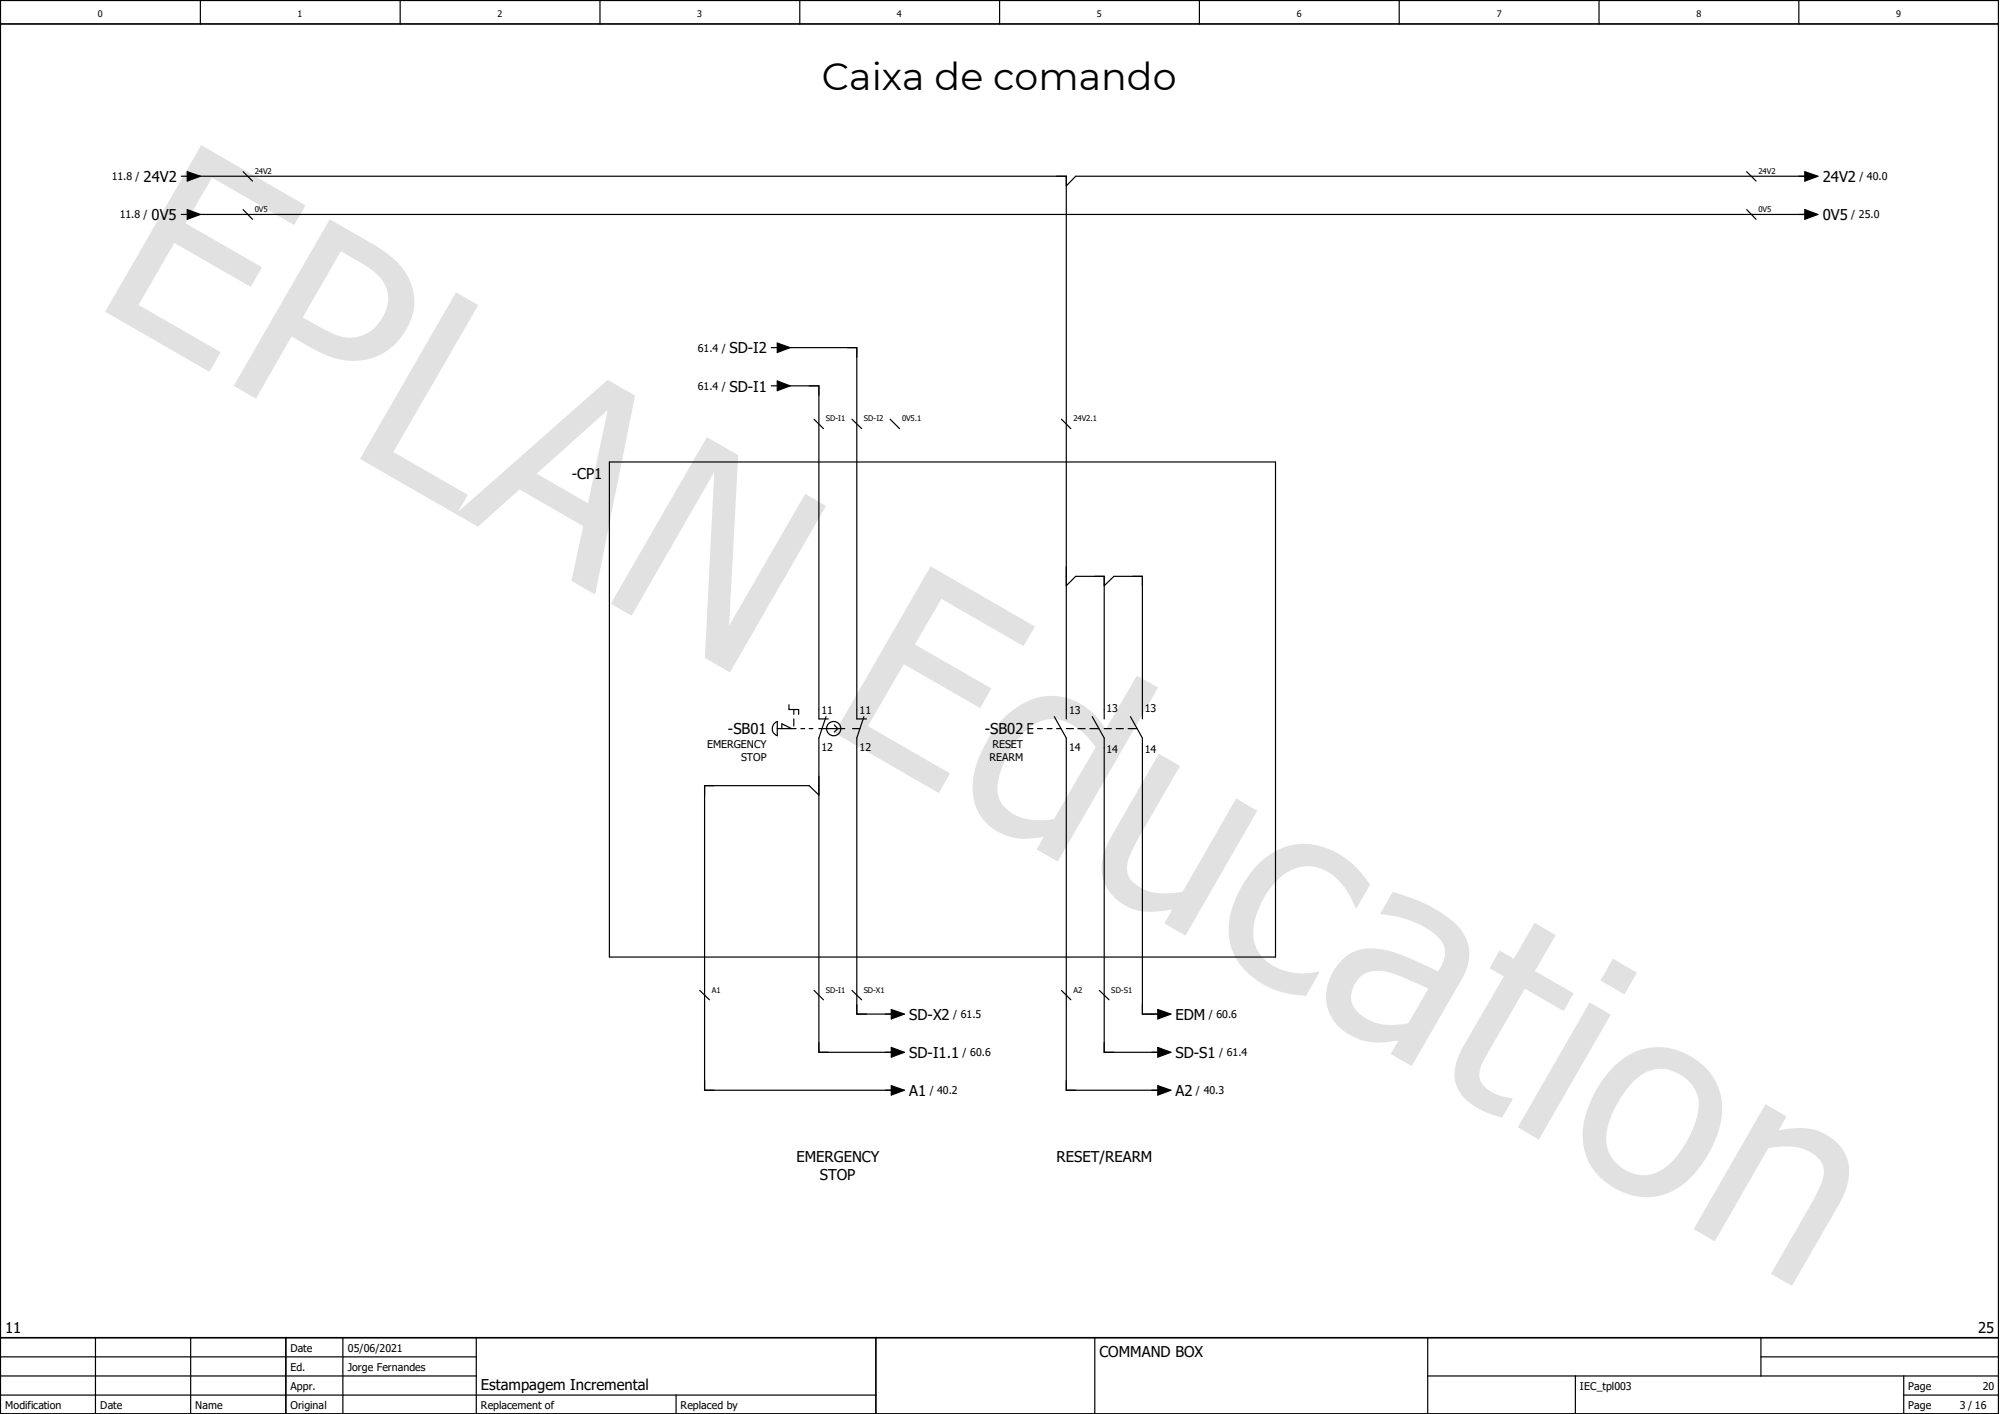
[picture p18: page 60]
EMERGENCY STOP; RESET/REARM; RESET REARM; EDM / 60.6

Date | 05/06/2021 | Estampagem Incremental | | COMMAND BOX
Ed. | Jorge Fernandes
Appr. | | | | | IEC_tpl003 | Page 20

Modification | Date | Name | Original | | Replacement of | Replaced by | | | | Page 3 / 16

## Alimentação controlador

Date | 05/06/2021 | Estampagem Incremental | | POWER SUPPLY PLC
Ed. | Jorge Fernandes
Appr. | | | | | IEC_tpl003 | Page 25

Modification | Date | Name | Original | | Replacement of | Replaced by | | | | Page 4 / 16

## Controlador

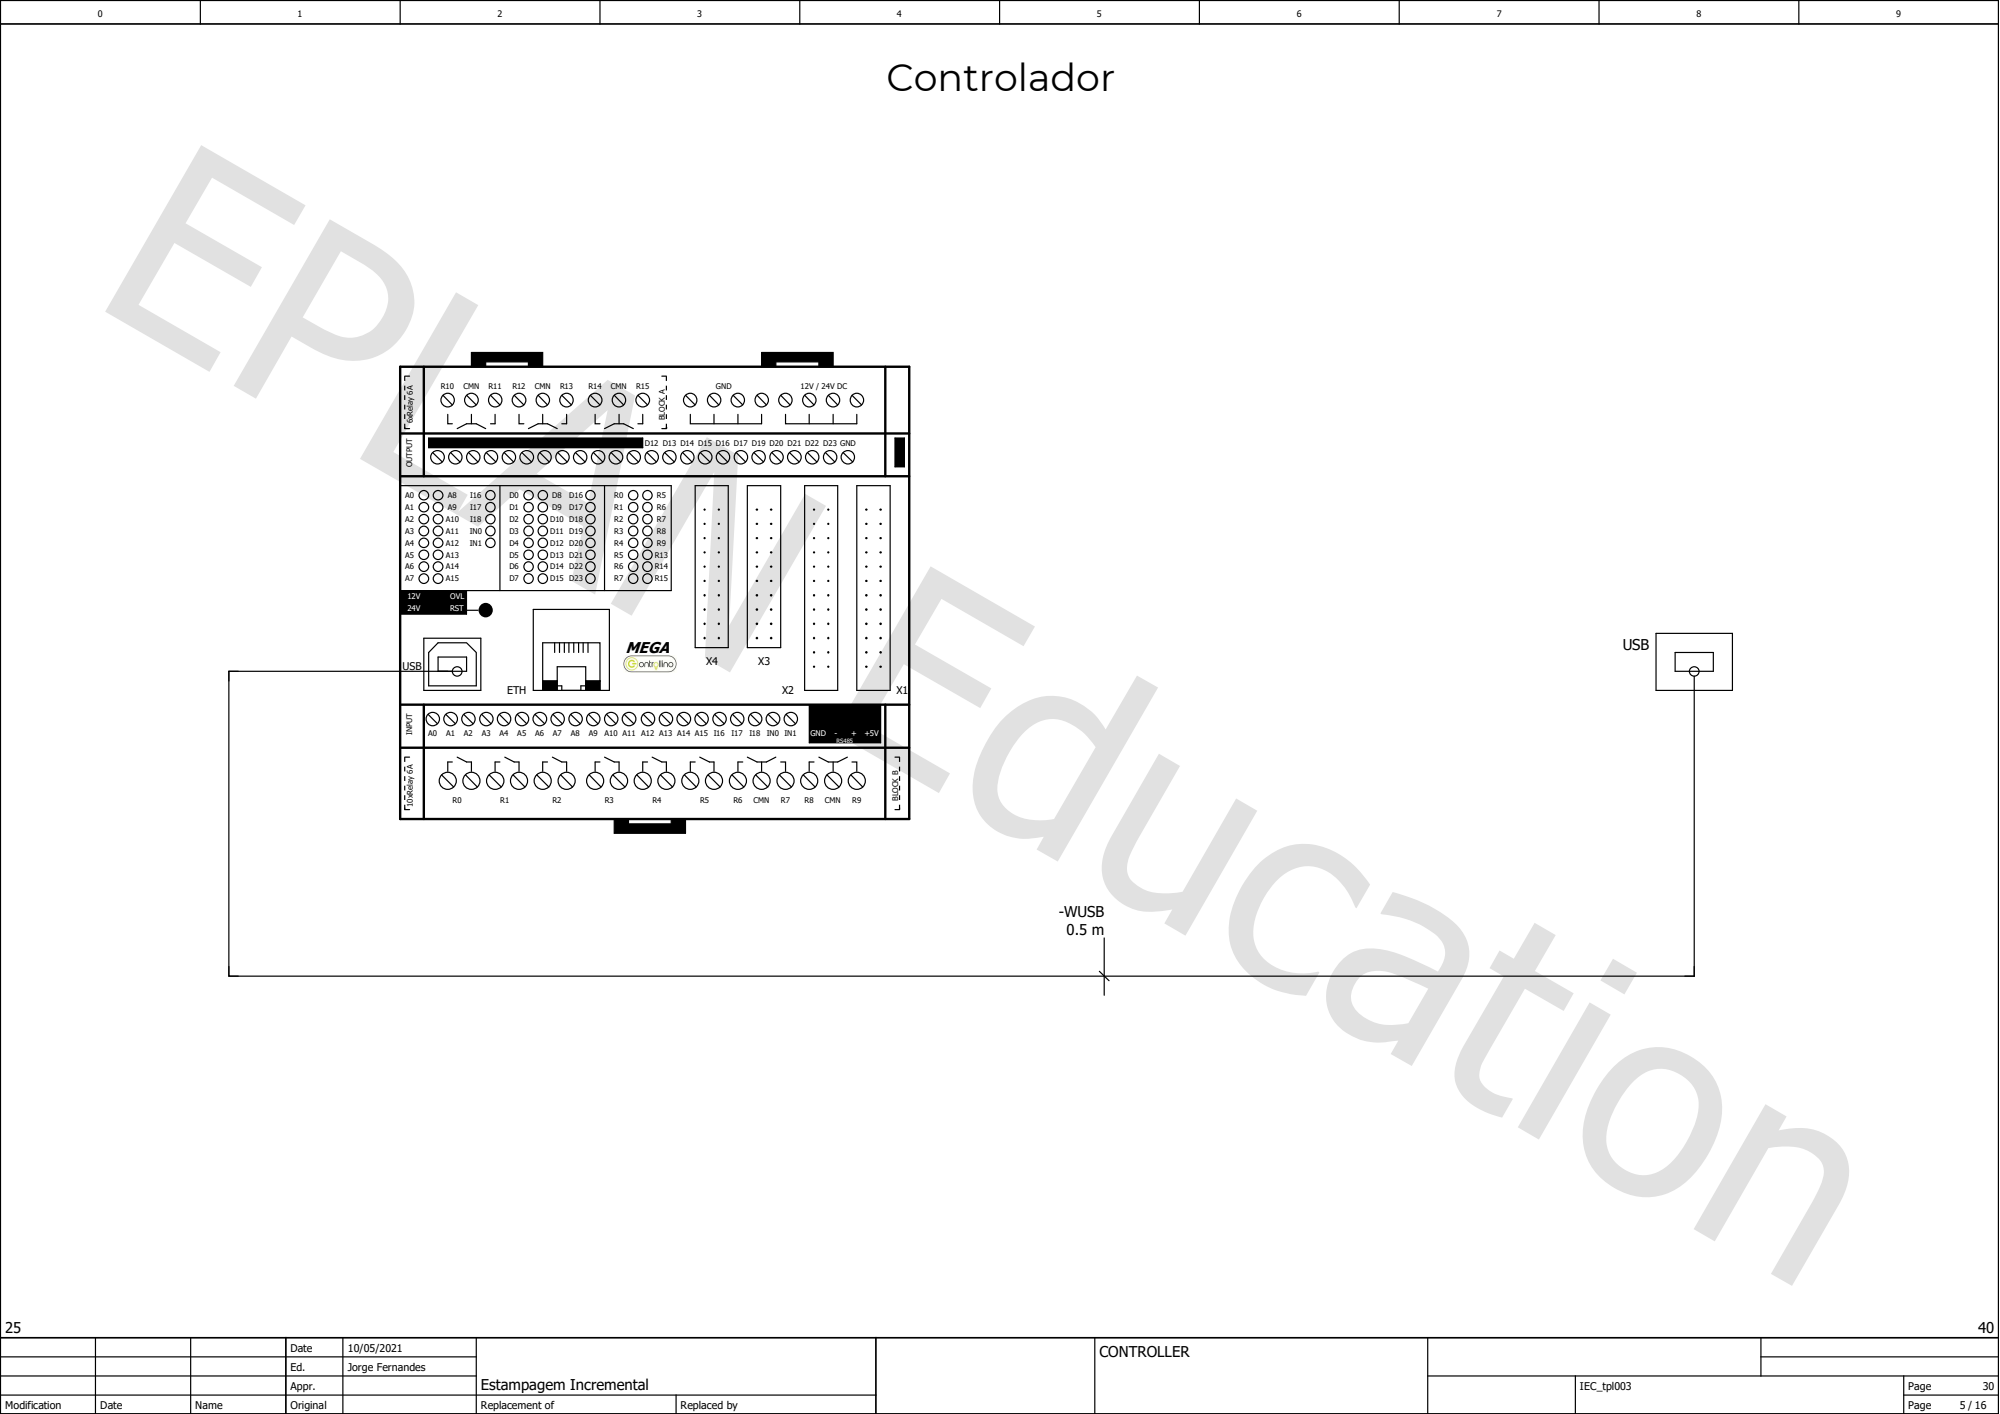
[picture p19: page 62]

Date | 10/05/2021 | Estampagem Incremental | | CONTROLLER
Ed. | Jorge Fernandes
Appr. | | | | | IEC_tpl003 | Page 30

Modification | Date | Name | Original | | Replacement of | Replaced by | | | | Page 5 / 16

## Entradas 1

Date | 05/06/2021 | Estampagem Incremental | | INPUT
Ed. | Jorge Fernandes
Appr. | | | | | IEC_tpl003 | Page 40

Modification | Date | Name | Original | | Replacement of | Replaced by | | | | Page 6 / 16

## Entradas 2

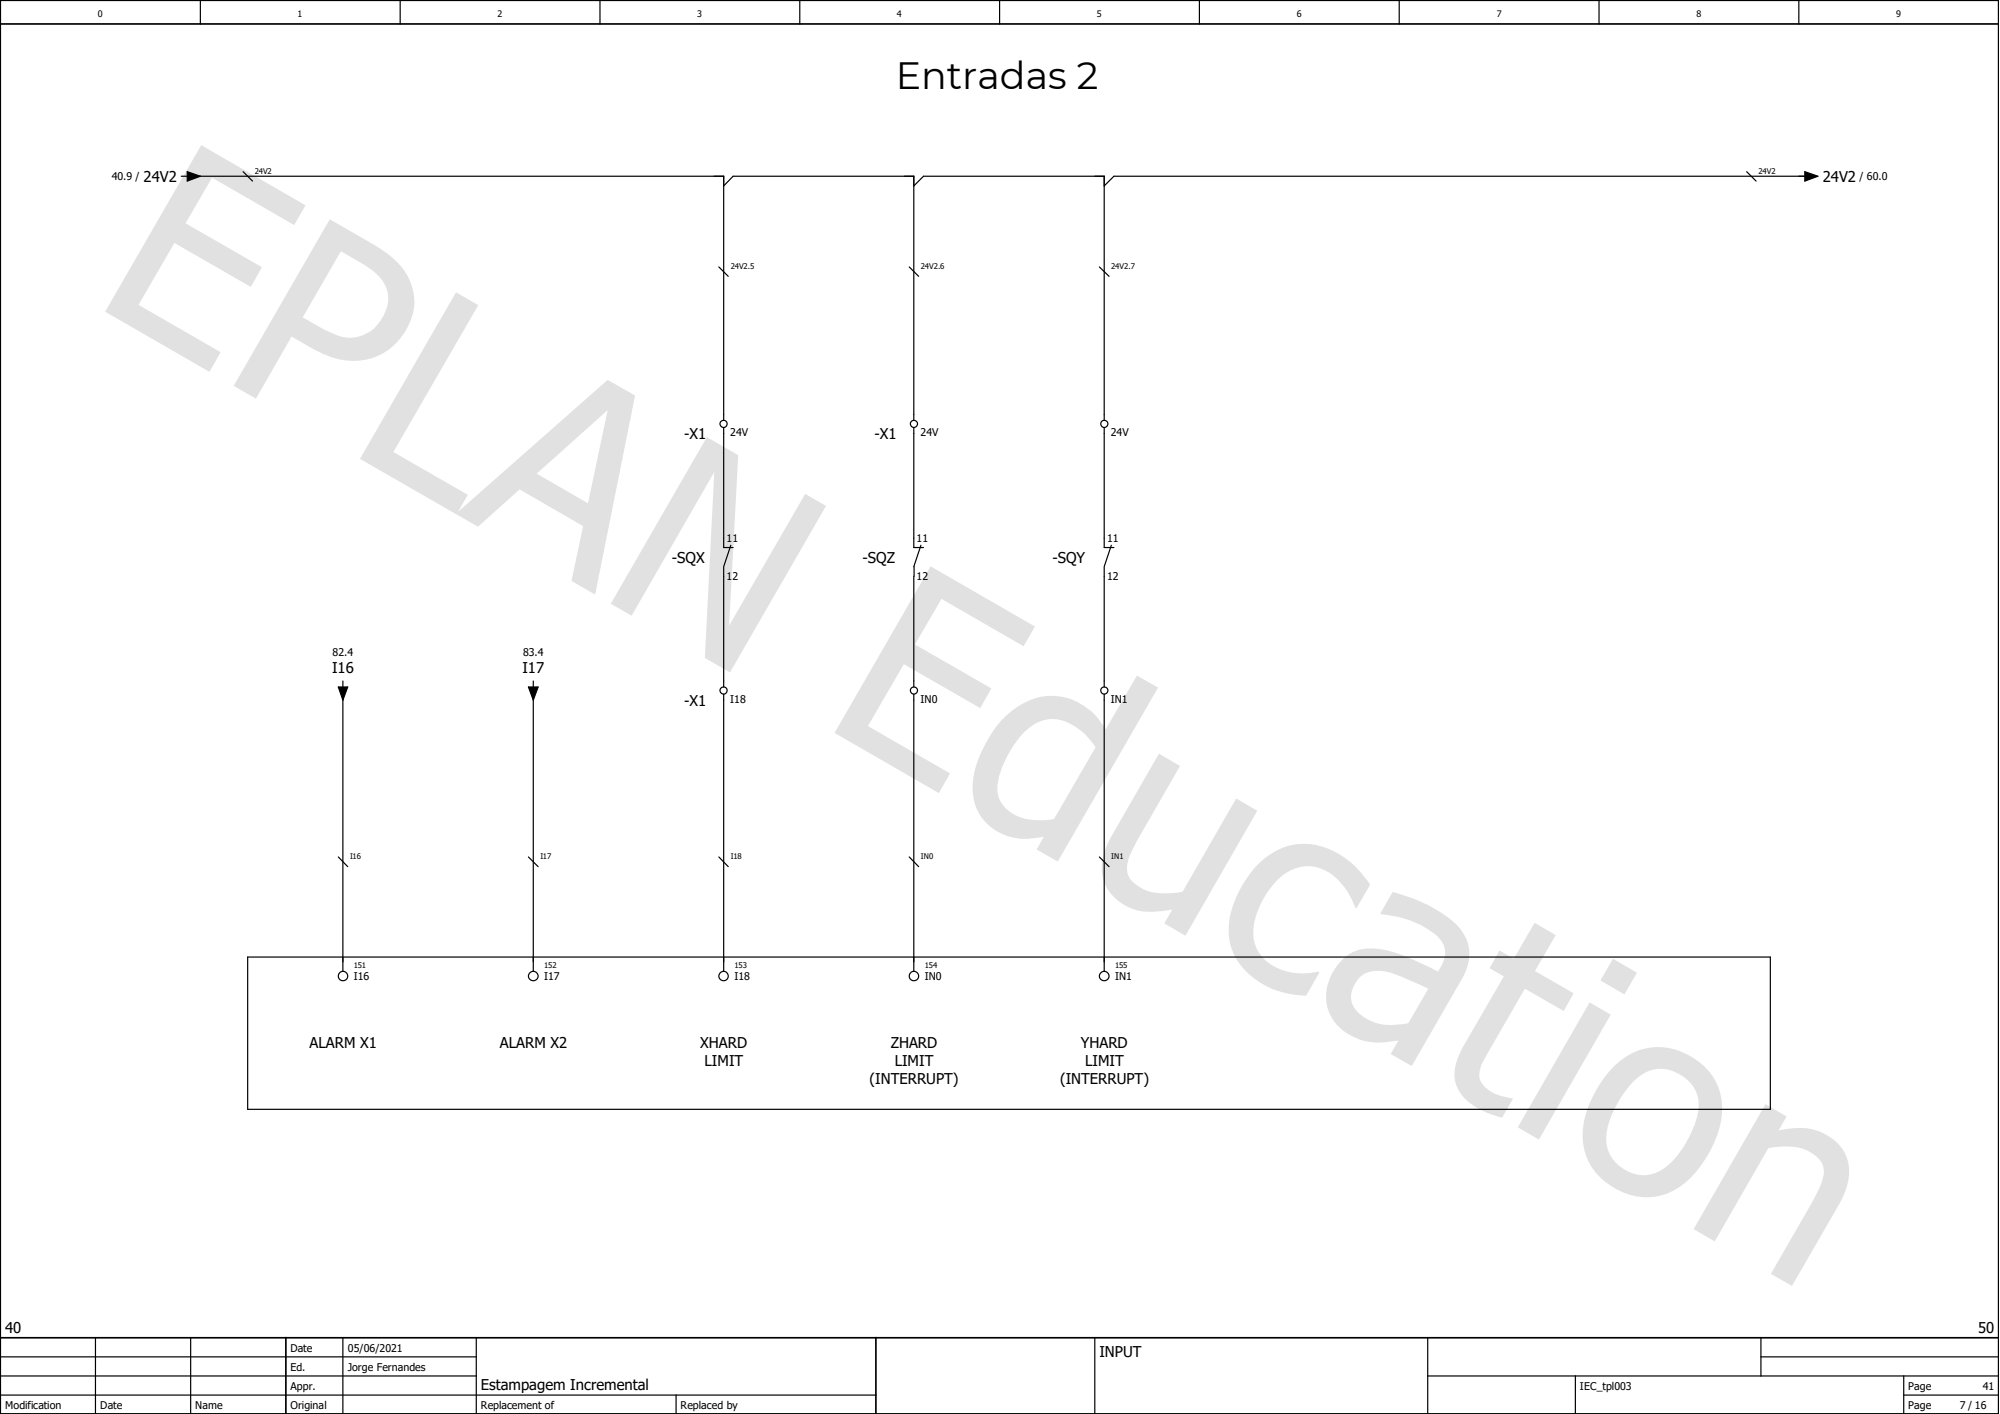
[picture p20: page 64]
XHARD LIMIT; ZHARD LIMIT (INTERRUPT); YHARD LIMIT (INTERRUPT); ALARM X1; ALARM X2; -SQZ; -SQY; -SQX

Date | 05/06/2021 | Estampagem Incremental | | INPUT
Ed. | Jorge Fernandes
Appr. | | | | | IEC_tpl003 | Page 41

Modification | Date | Name | Original | | Replacement of | Replaced by | | | | Page 7 / 16

## Saídas 1

Date | 10/05/2021 | Estampagem Incremental | | OUTPUT
Ed. | Jorge Fernandes
Appr. | | | | | IEC_tpl003 | Page 50

Modification | Date | Name | Original | | Replacement of | Replaced by | | | | Page 8 / 16

## Saídas 2

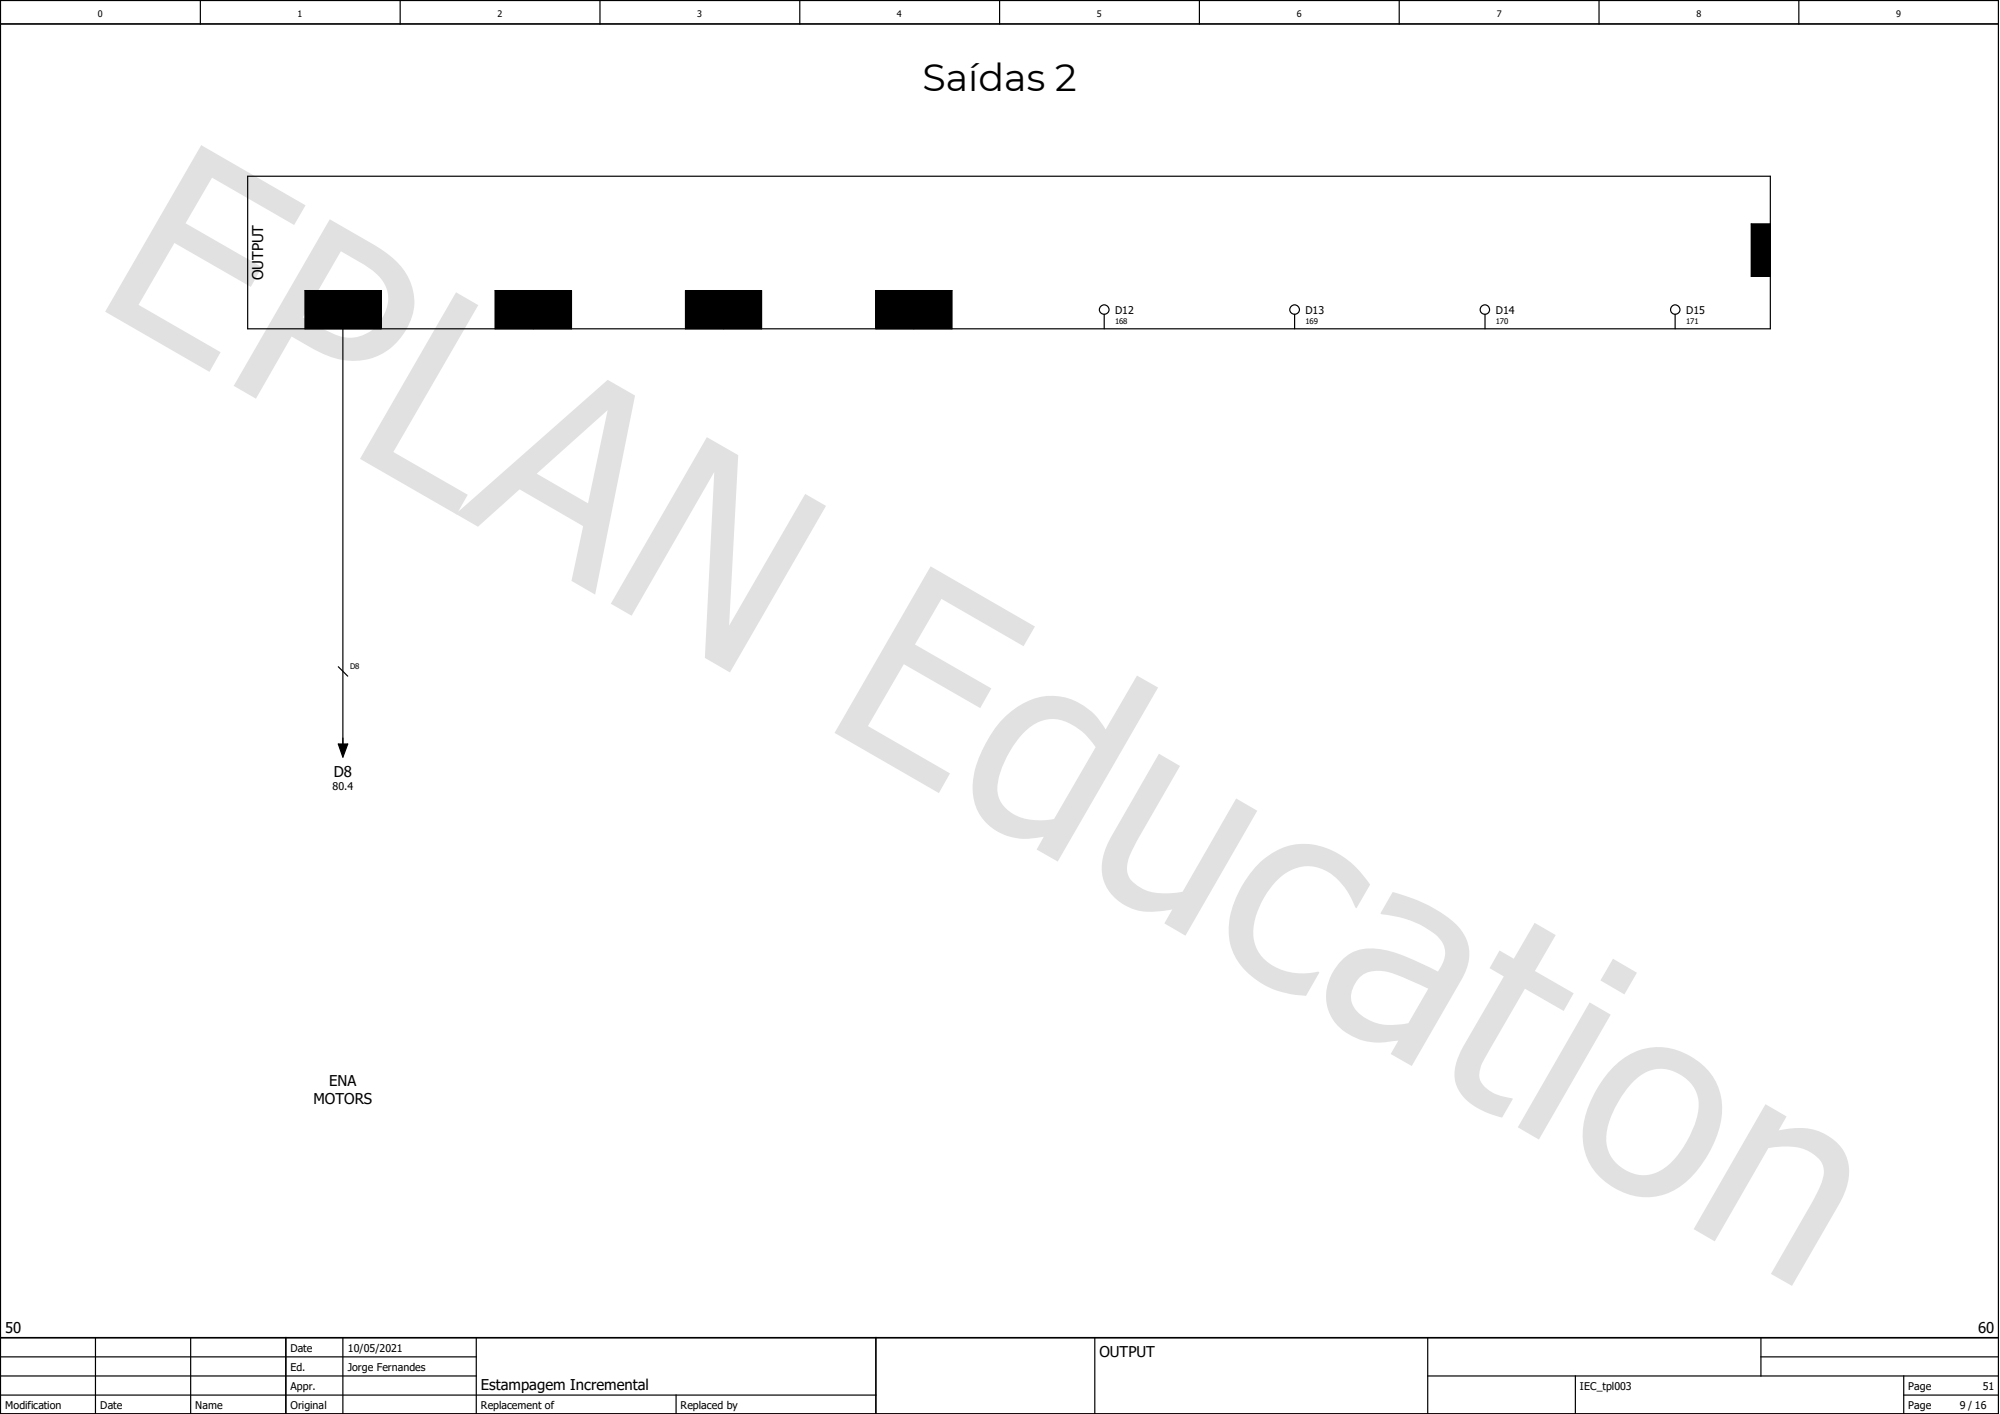
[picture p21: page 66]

Date | 10/05/2021 | Estampagem Incremental | | OUTPUT
Ed. | Jorge Fernandes
Appr. | | | | | IEC_tpl003 | Page 51

Modification | Date | Name | Original | | Replacement of | Replaced by | | | | Page 9 / 16

## Barreira imaterial

Date | 05/06/2021 | Estampagem Incremental | | LIGHT BARRIER
Ed. | Jorge Fernandes
Appr. | | | | | IEC_tpl003 | Page 60

Modification | Date | Name | Original | | Replacement of | Replaced by | | | | Page 10 / 16

## Relé de segurança

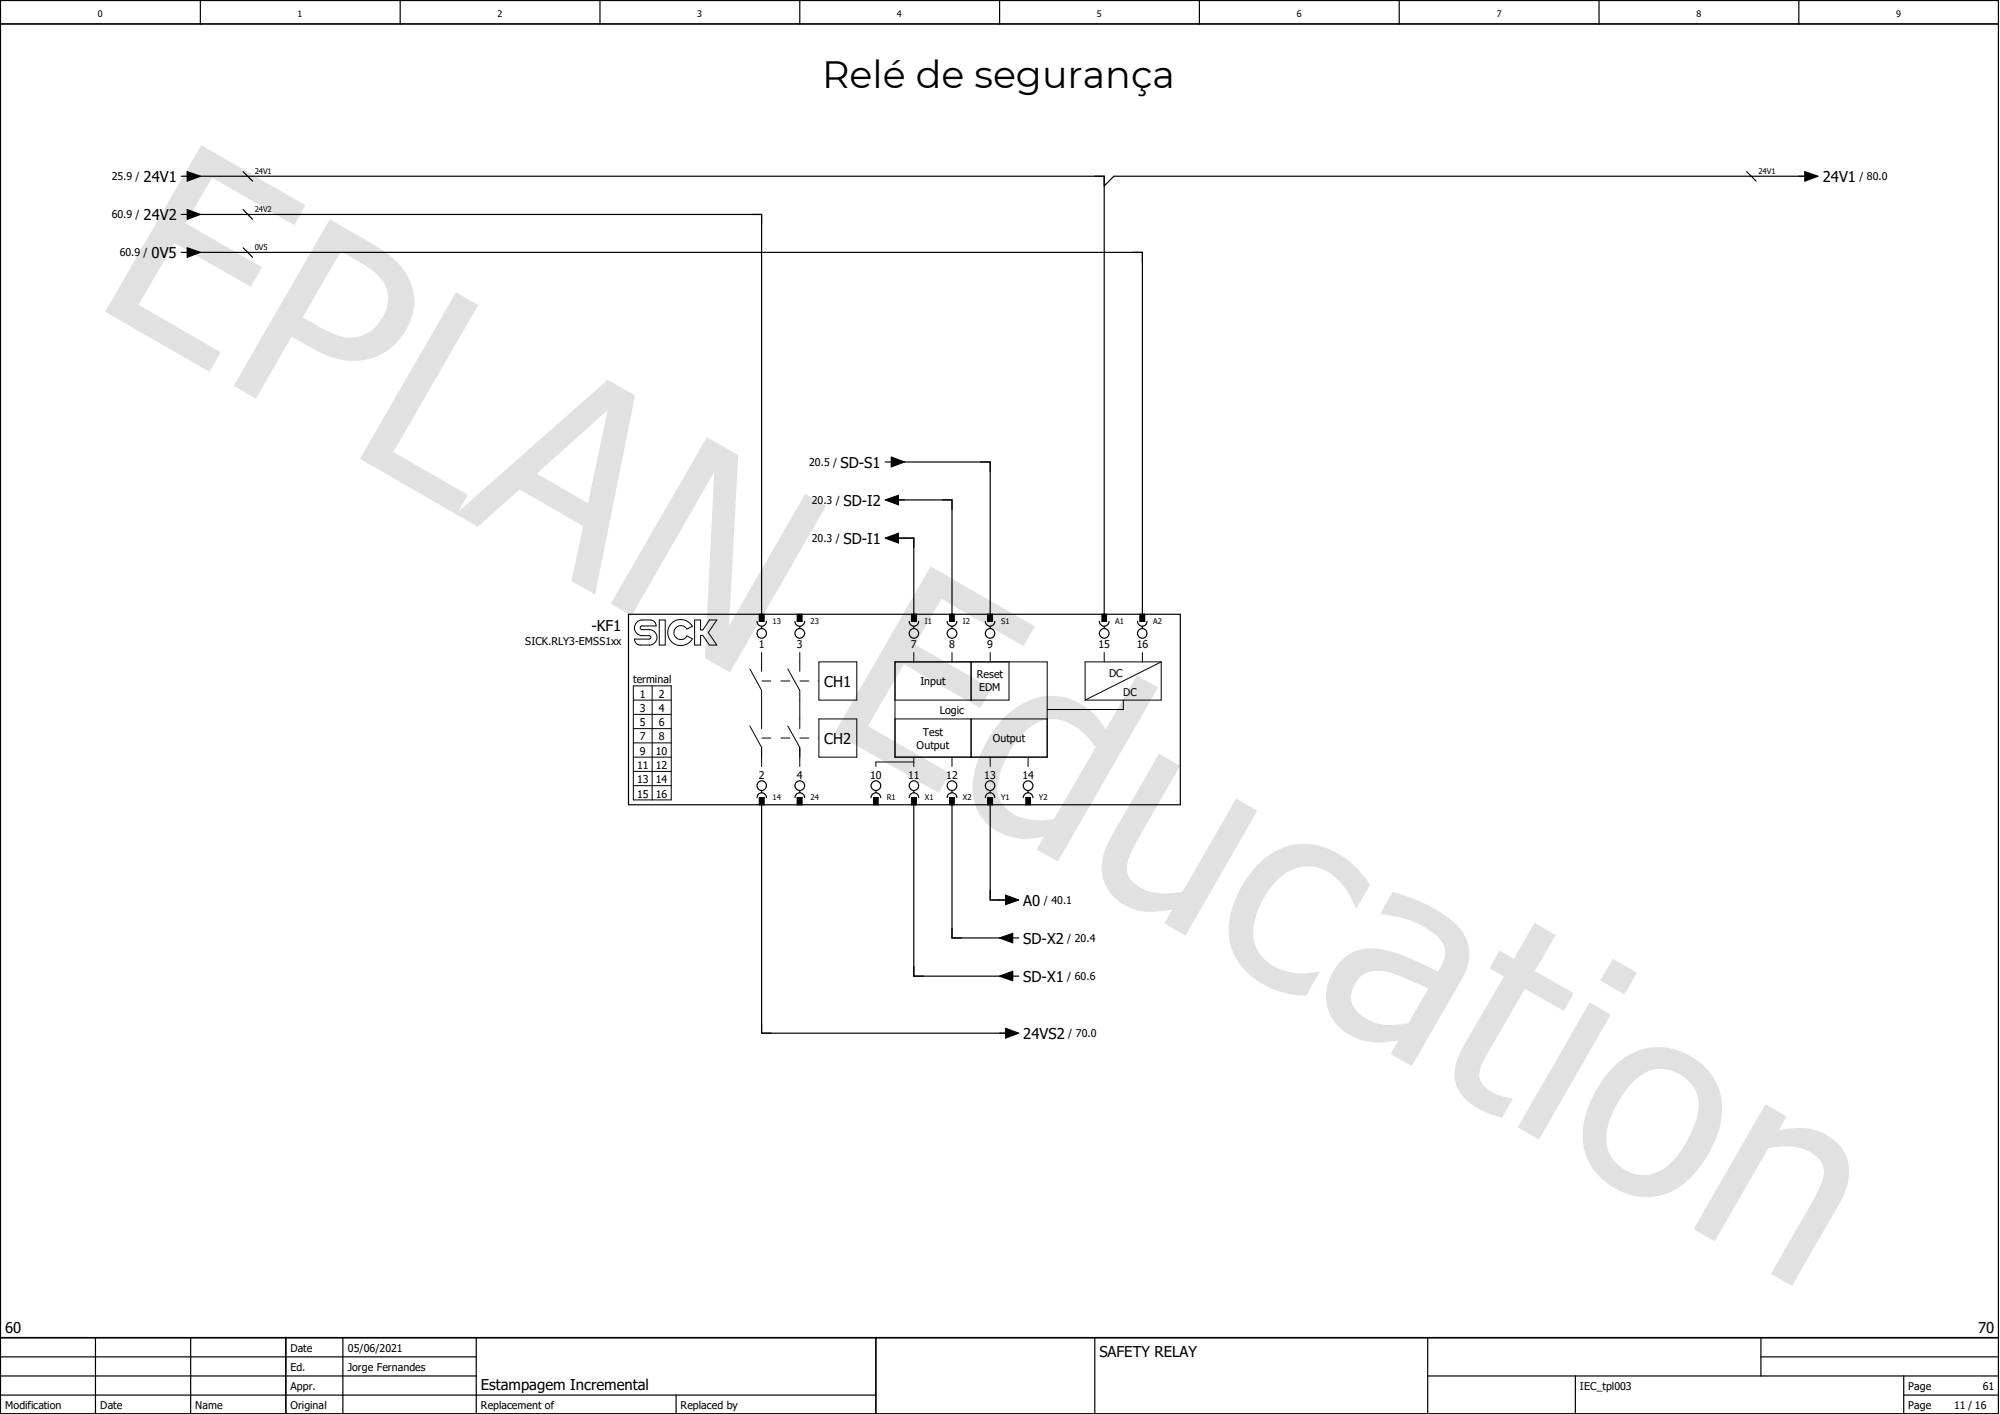
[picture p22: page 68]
Logic; Reset EDM; Input; terminal; SICK.RLY3-EMSS1xx

Output Test Output

11 | 12 | 10 11 12 13 14 R1 X1 X2 Y1 Y2
13 | 14
15 | 16

Date | 05/06/2021 | Estampagem Incremental | | SAFETY RELAY
Ed. | Jorge Fernandes
Appr. | | | | | IEC_tpl003 | Page 61

Modification | Date | Name | Original | | Replacement of | Replaced by | | | | Page 11 / 16

## Ativação e controlo

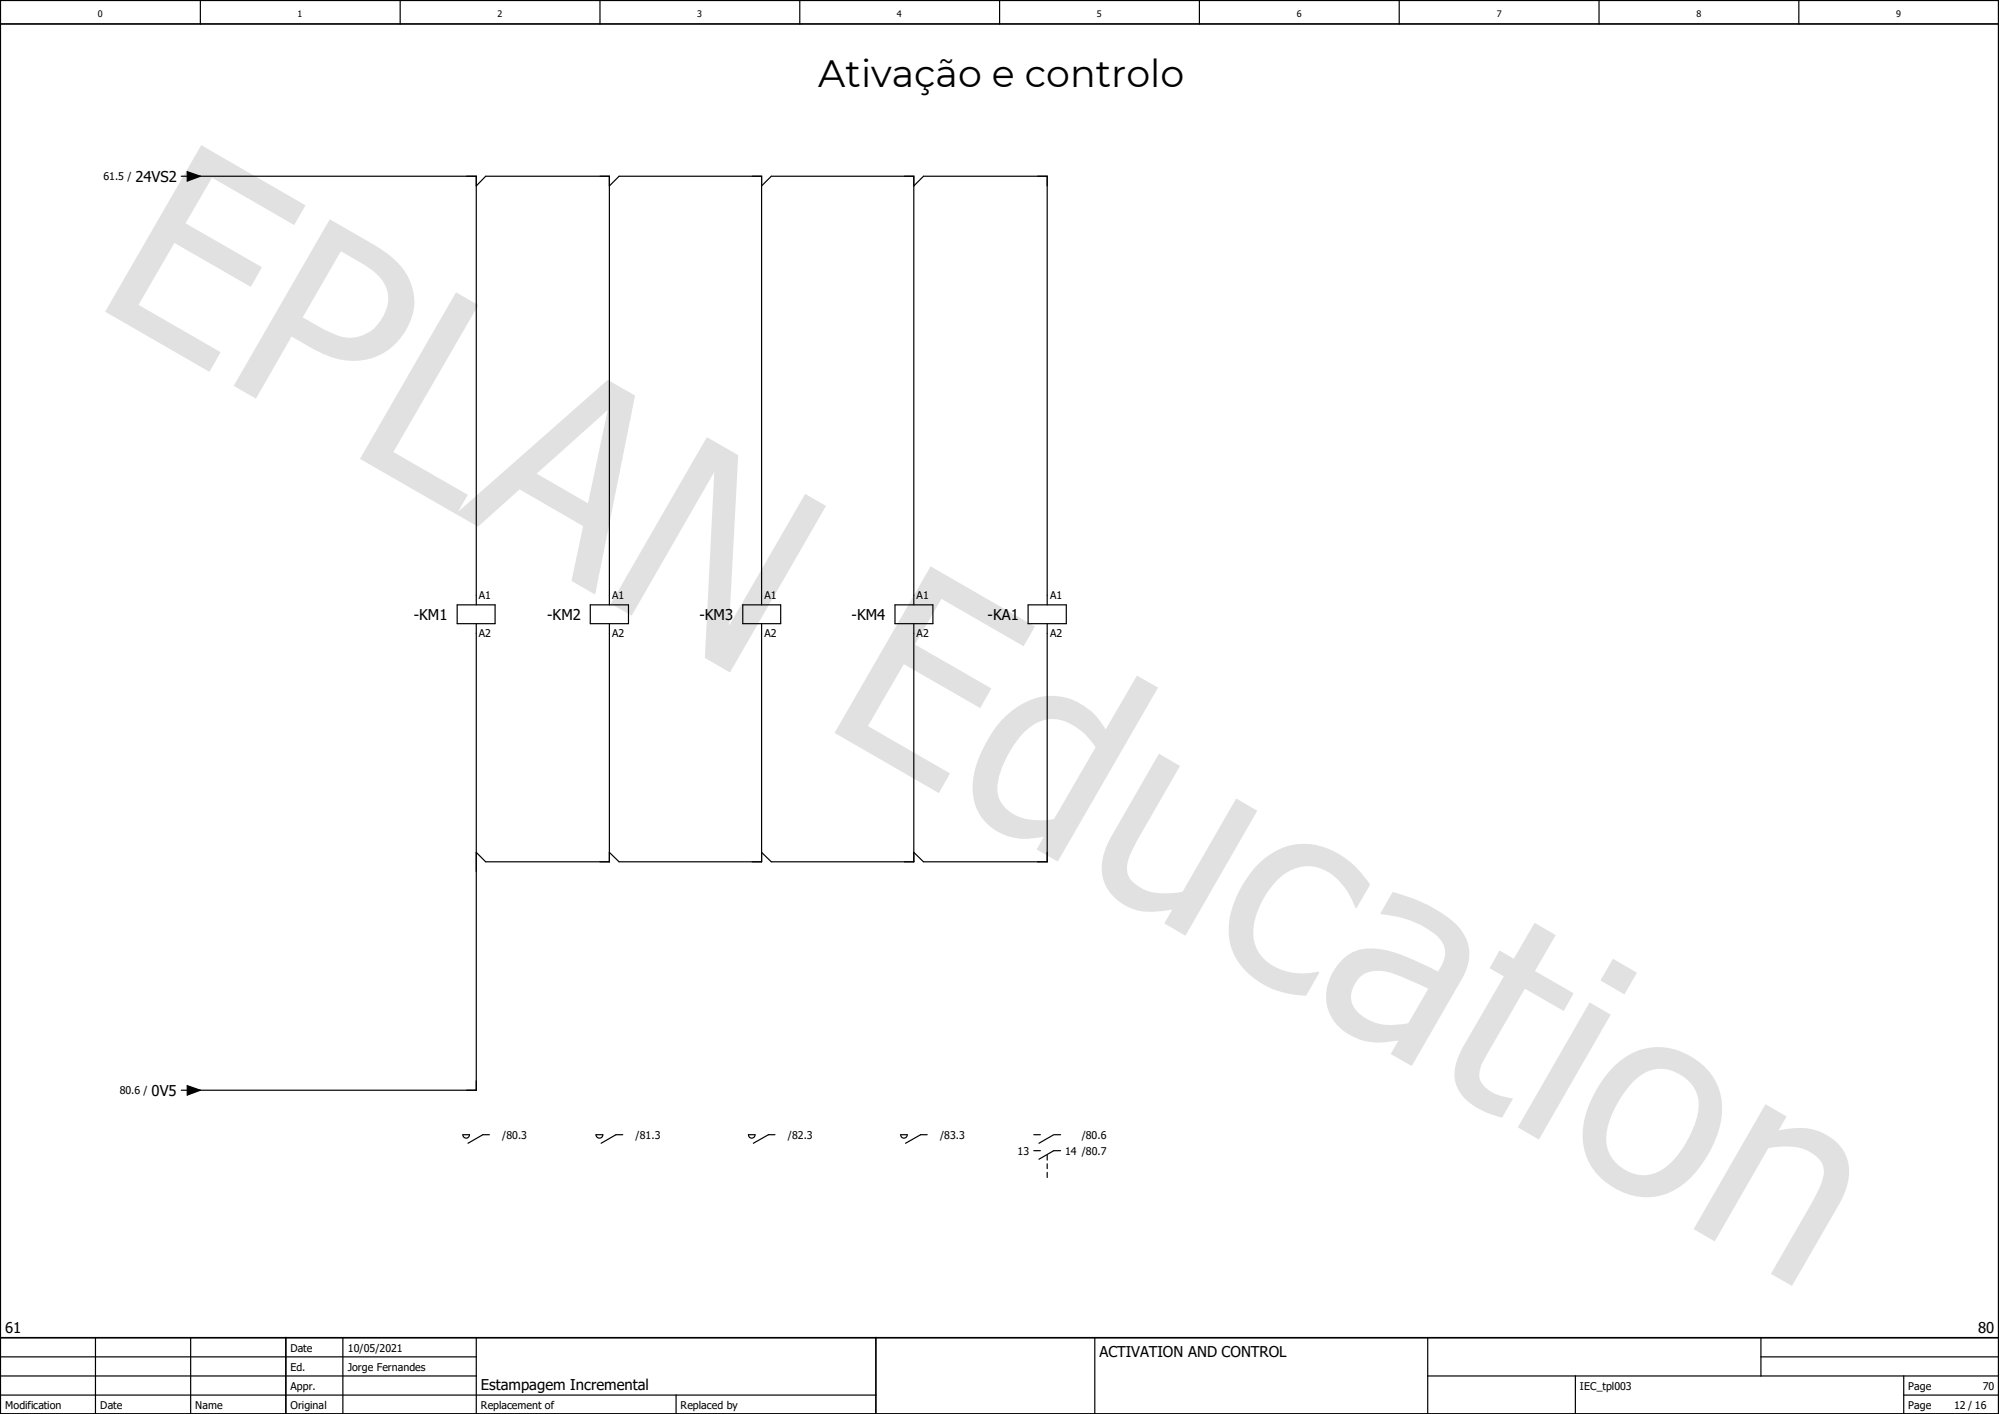
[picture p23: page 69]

Date | 10/05/2021 | Estampagem Incremental | | ACTIVATION AND CONTROL
Ed. | Jorge Fernandes
Appr. | | | | | IEC_tpl003 | Page 70

Modification | Date | Name | Original | | Replacement of | Replaced by | | | | Page 12 / 16

## Driver eixo Z

Z AXIS MOTOR + ENCODER + BRAKE

RELÉ
ACIONAMENTO
TRAVÃO
(ABRE PARA ACIONAR O TRAVÃO)

Date | 10/05/2021 | Estampagem Incremental | | Z AXIS DRIVER
Ed. | Jorge Fernandes
Appr. | | | | | IEC_tpl003 | Page 80

Modification | Date | Name | Original | | Replacement of | Replaced by | | | | Page 13 / 16

## Driver eixo Y

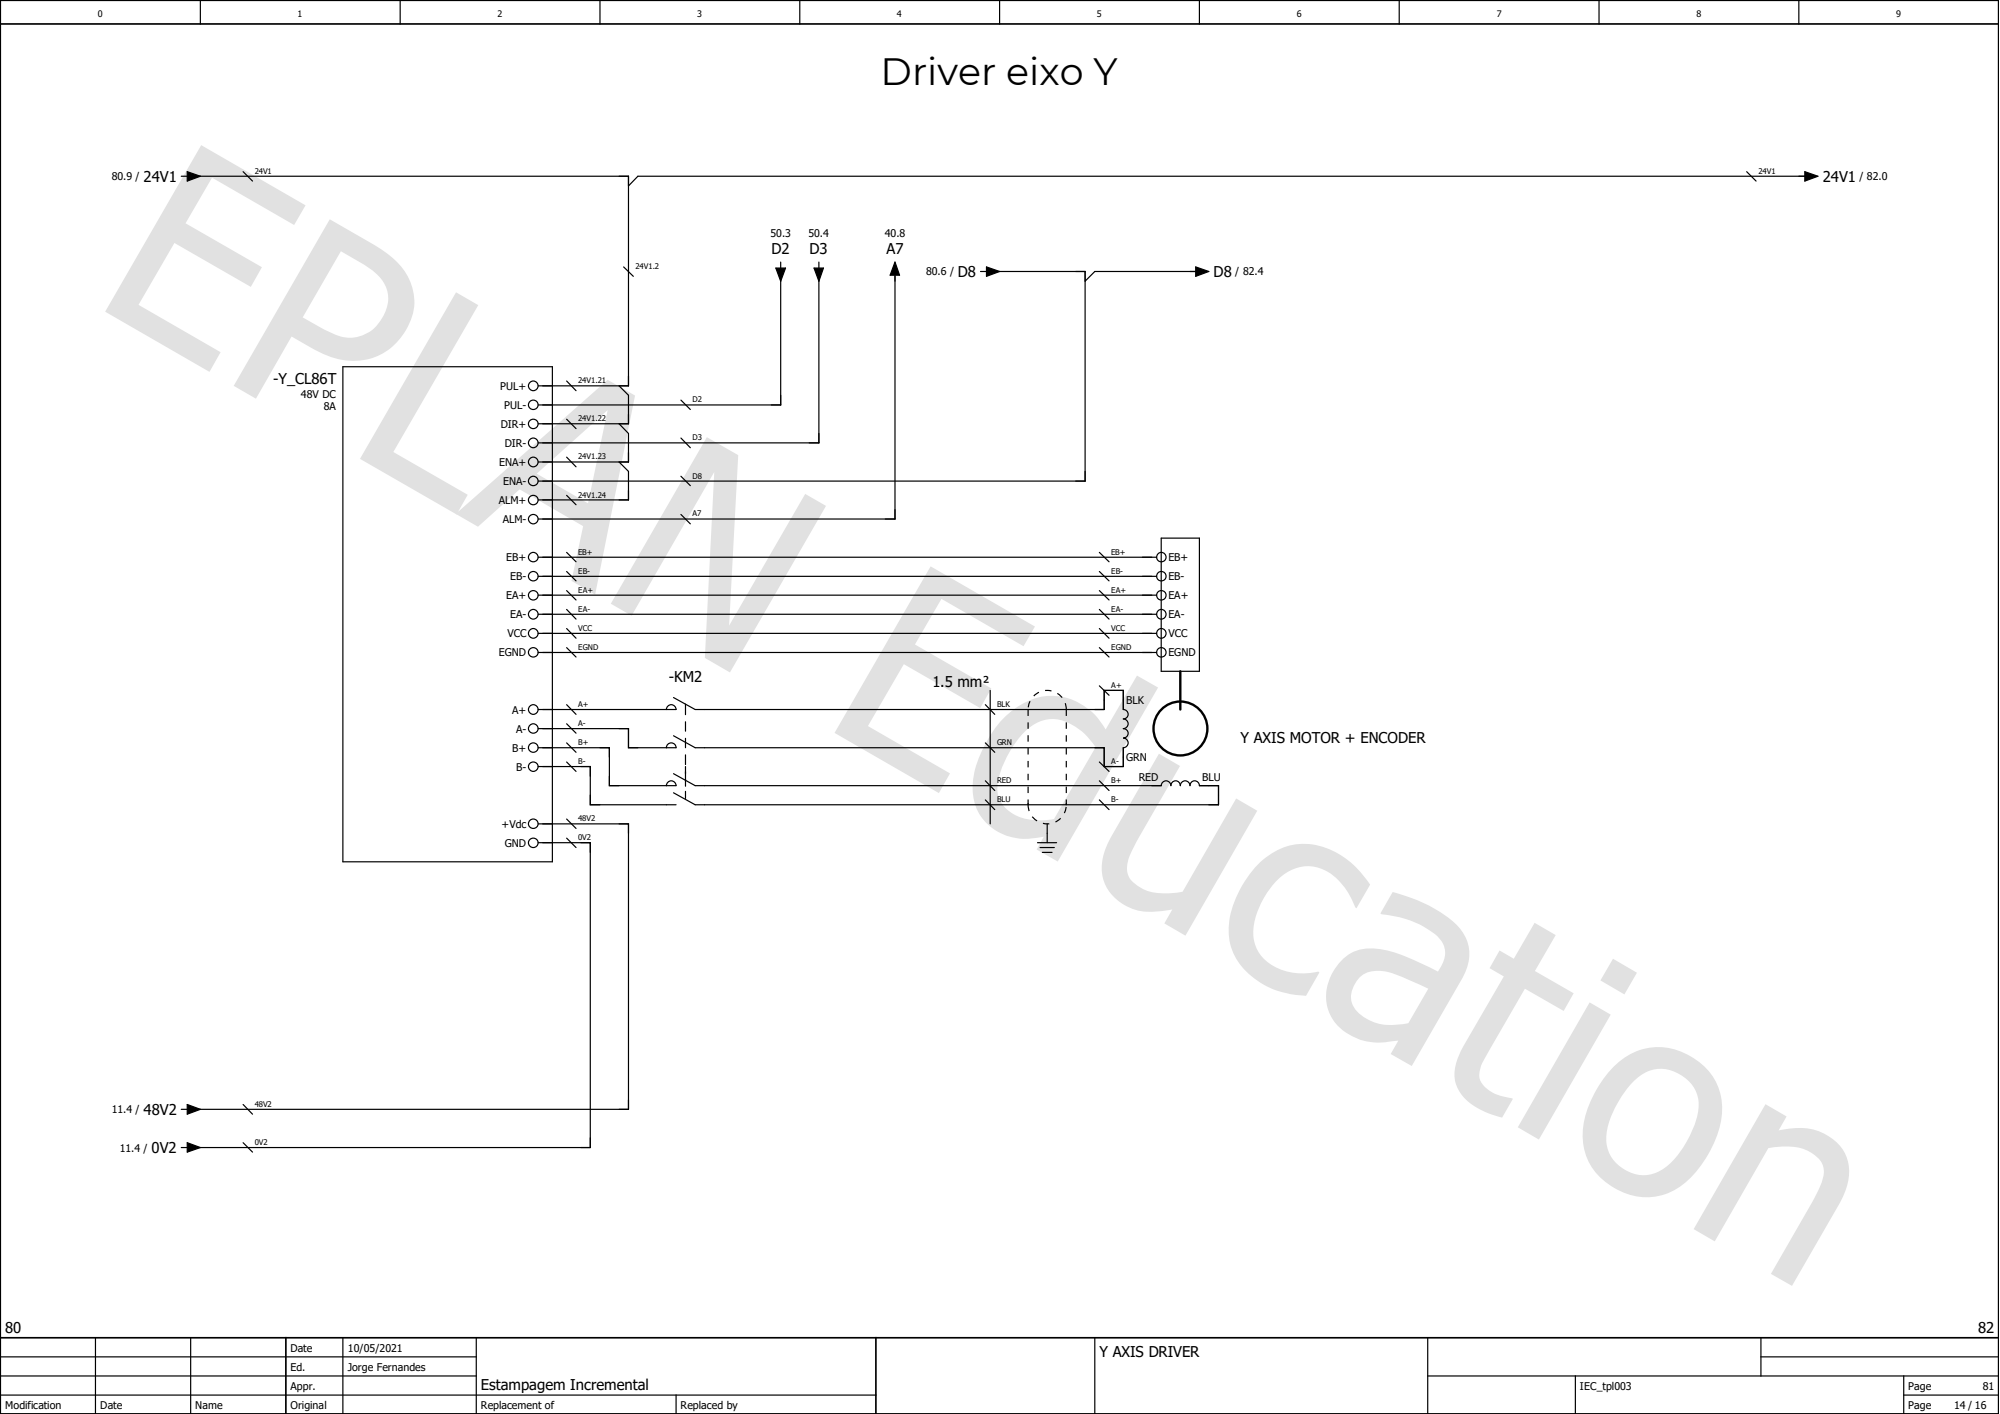
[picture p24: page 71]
PUL+; PUL-; DIR+; DIR-; ENA+; ENA-; ALM+; ALM-; VCC; EGND; +Vdc; GND; BLK; GRN; RED; BLU; 1.5 mm²

Y AXIS MOTOR + ENCODER

Date | 10/05/2021 | Estampagem Incremental | | Y AXIS DRIVER
Ed. | Jorge Fernandes
Appr. | | | | | IEC_tpl003 | Page 81

Modification | Date | Name | Original | | Replacement of | Replaced by | | | | Page 14 / 16

## Driver eixo X1

X1 AXIS MOTOR + ENCODER

Date | 10/05/2021 | Estampagem Incremental | | X1 AXIS DRIVER
Ed. | Jorge Fernandes
Appr. | | | | | IEC_tpl003 | Page 82

Modification | Date | Name | Original | | Replacement of | Replaced by | | | | Page 15 / 16

## Driver eixo X2

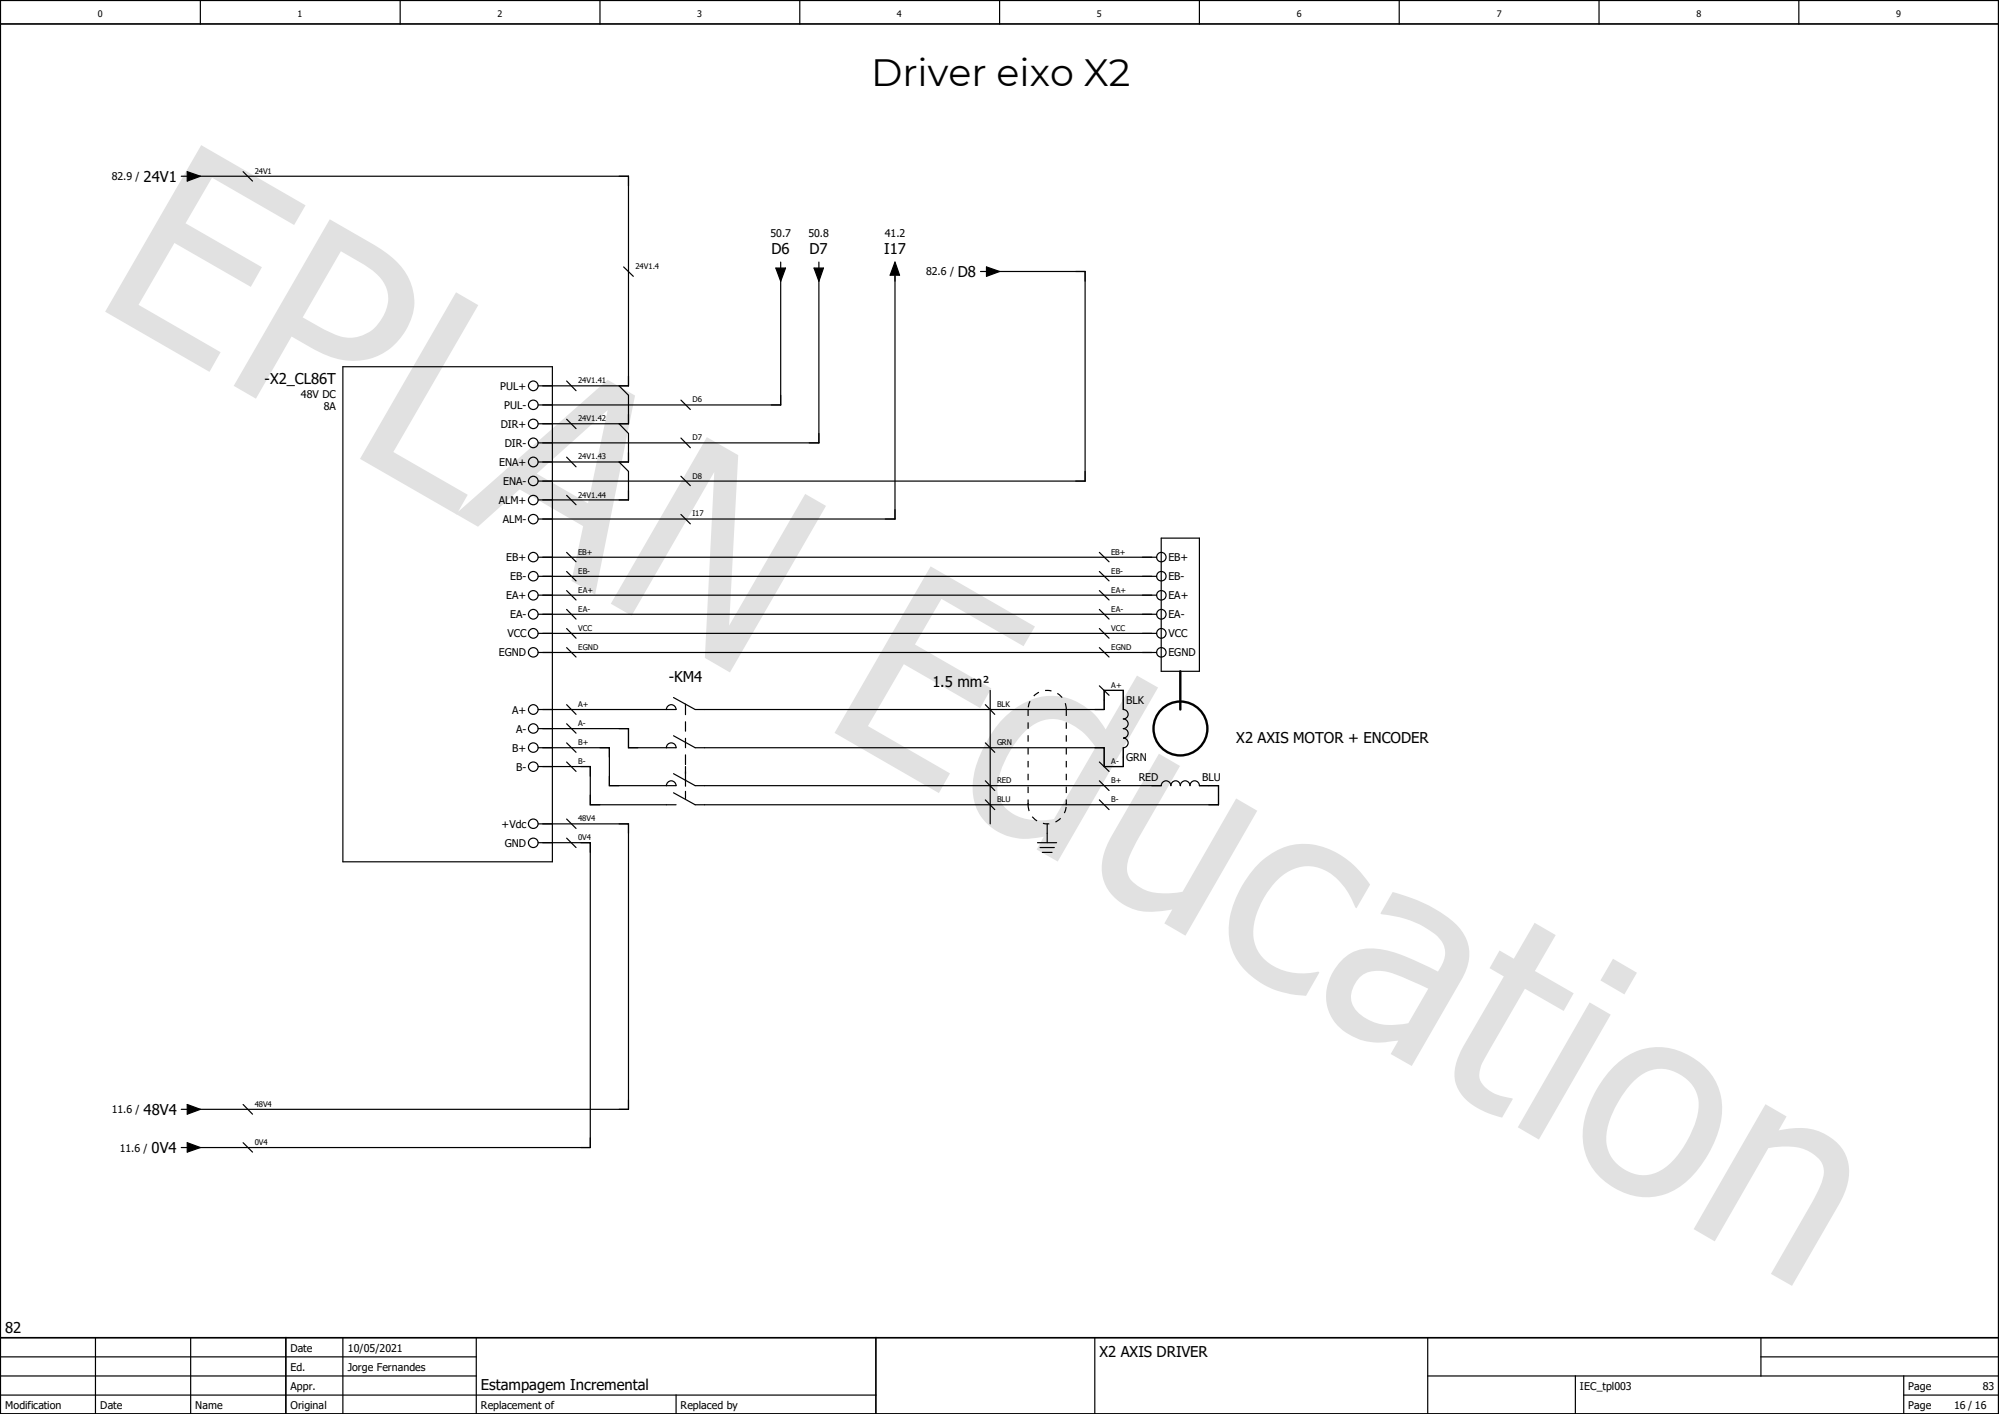
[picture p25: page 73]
PUL+; PUL-; DIR+; DIR-; ENA+; ENA-; ALM+; ALM-; VCC; EGND; +Vdc; GND; BLK; GRN; RED; BLU; 1.5 mm²

X2 AXIS MOTOR + ENCODER

Date | 10/05/2021 | Estampagem Incremental | | X2 AXIS DRIVER
Ed. | Jorge Fernandes
Appr. | | | | | IEC_tpl003 | Page 83

Modification | Date | Name | Original | | Replacement of | Replaced by | | | | Page 16 / 16

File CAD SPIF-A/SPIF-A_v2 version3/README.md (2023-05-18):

Version 2 of the SPIF:

- Defined architecture
- Selected Binding Components
- Simulation of selected components
- Reorganizing Folders in the Assembly
- Reinforcement of the robot structure
- Added tool holder
- New component simulation
- Selection of resuctors
- Implementation of reducers in the system
- Linear module selection
- Implementation of the linear module
- Addition of structure
- Structure simulation
- Adding the electrical panel



Links:
- [Assembly](https://uapt33090-my.sharepoint.com/:u:/g/personal/tatianaresende_ua_pt/EYB6fhaDQr1PjClM0OEuDzoB3Mrge2ubZzzEQG7Tr5ImUQ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)
- [Folder with all parts](https://uapt33090-my.sharepoint.com/:f:/g/personal/tatianaresende_ua_pt/EkW3uTSmKChHud8DiJhO23MBPe5fX8kKzHM7XouAHOt3sg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)
- [Folder with the simulation](https://uapt33090-my.sharepoint.com/:f:/g/personal/tatianaresende_ua_pt/EriKW3PNY01Gs3kQlUSw3cwBOAway57NYBCUWKuT_qRx2A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)

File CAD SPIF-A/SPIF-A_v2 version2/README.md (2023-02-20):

Version 2 of the SPIF:
- Defined architecture
- Selected binding components
- Simulation of selected components
- Reorganization of folders in the assembly
- Reinforcement of the structure
- Added toolholder
- New simulation of components



Link to assembly:
[https://uapt33090-my.sharepoint.com/:u:/g/personal/tatianaresende_ua_pt/Ef8z9VNXxRFNqxFwtq_23vwBvoqPO6ZGOpv9yMJB7fl3aA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](https://uapt33090-my.sharepoint.com/:u:/g/personal/tatianaresende_ua_pt/EWpSwhBv405DmJp2mrbMTxIBs2UiLfg5EcQ6swdn1y45ug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)

Folder with the simulation:
[https://uapt33090-my.sharepoint.com/:f:/g/personal/tatianaresende_ua_pt/EhnLqy7rWW9Jpvjzhjw4m4YBRr73Z7guXcKzM642BJGIMg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](https://uapt33090-my.sharepoint.com/:f:/g/personal/tatianaresende_ua_pt/EphbLRSx30lJgPIjIdGg-AoBC33HVcpTUeXvhgUQe4Lp6g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)

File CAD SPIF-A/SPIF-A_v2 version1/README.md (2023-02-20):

Version 1 of the SPIF:
- Defined architecture
- Selected binding components
- Simulation of selected components

 

Link to assembly:
https://uapt33090-my.sharepoint.com/:u:/g/personal/tatianaresende_ua_pt/Ef8z9VNXxRFNqxFwtq_23vwBvoqPO6ZGOpv9yMJB7fl3aA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

Folder with the simulation:
https://uapt33090-my.sharepoint.com/:f:/g/personal/tatianaresende_ua_pt/EhnLqy7rWW9Jpvjzhjw4m4YBRr73Z7guXcKzM642BJGIMg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

Folder with some simulation images:
https://uapt33090-my.sharepoint.com/:f:/g/personal/tatianaresende_ua_pt/EhnLqy7rWW9Jpvjzhjw4m4YBRr73Z7guXcKzM642BJGIMg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

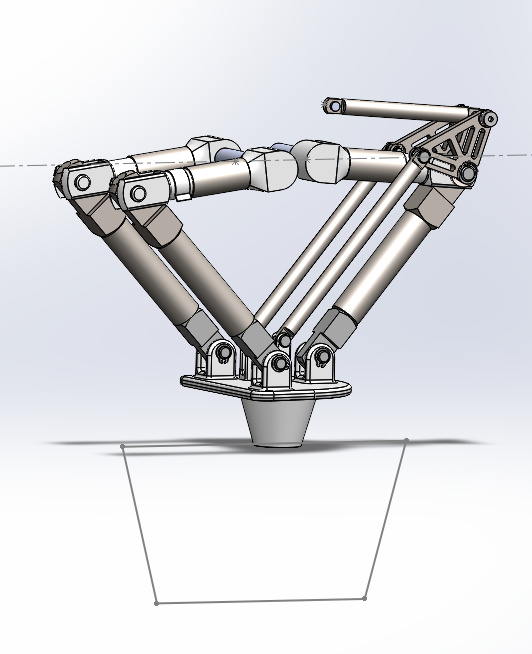
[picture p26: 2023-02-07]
images/SPIF-A_v2 version1.png

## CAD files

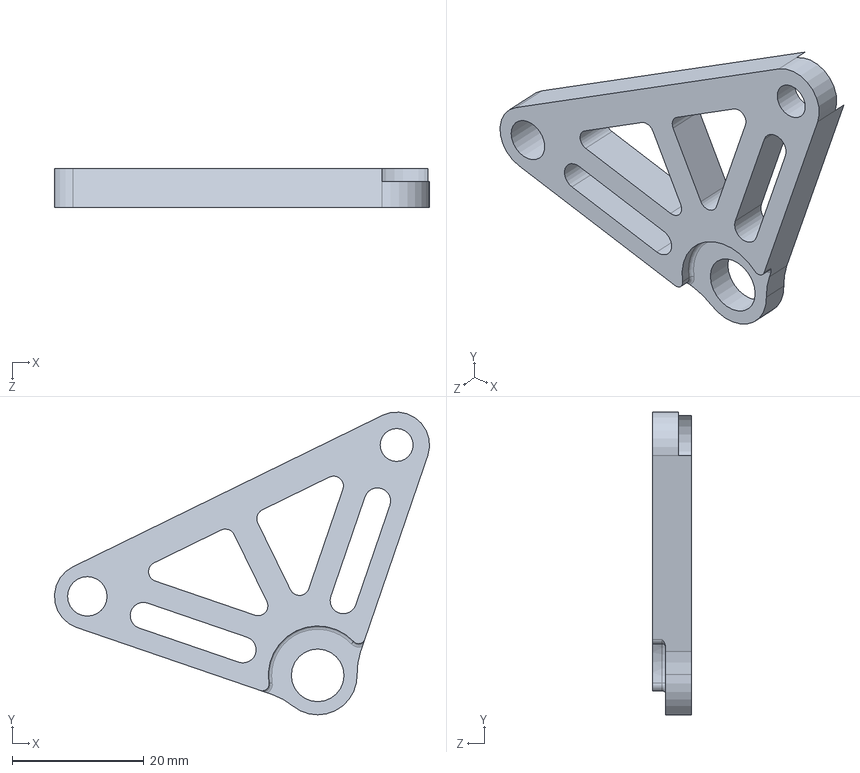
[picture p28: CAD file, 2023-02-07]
CAD SPIF-A/SPIF-A_v2 version1/componentes of mine/LigBarraParalelograma_2.SLDPRT
57.0 x 46.0 x 6.00 mm

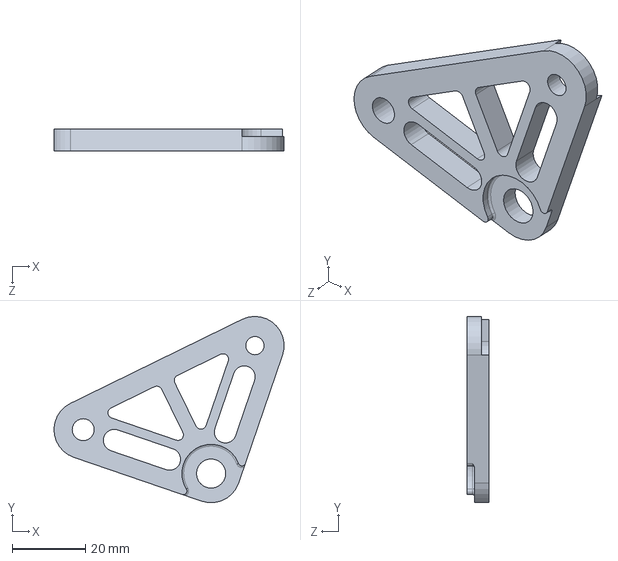
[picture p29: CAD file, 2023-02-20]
CAD SPIF-A/SPIF-A_v2 version2/Pecas Minhas/LigBarraParalelograma_2.SLDPRT
63.0 x 51.0 x 6.00 mm

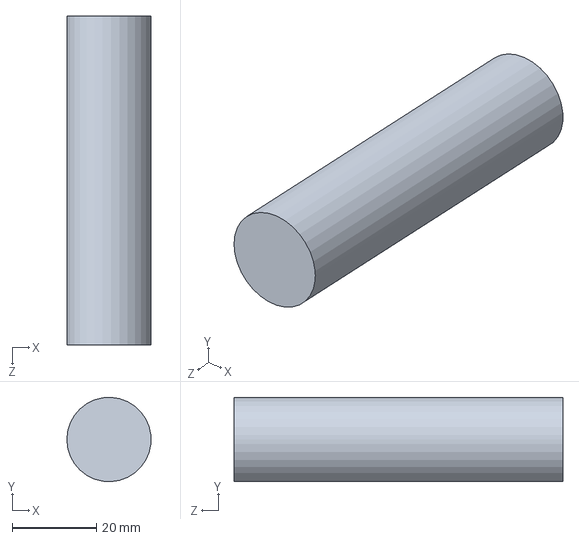
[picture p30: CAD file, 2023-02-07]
CAD SPIF-A/SPIF-A_v2 version1/componentes of mine/PerfilRedondo_20_130.SLDPRT
20.0 x 20.0 x 78.0 mm

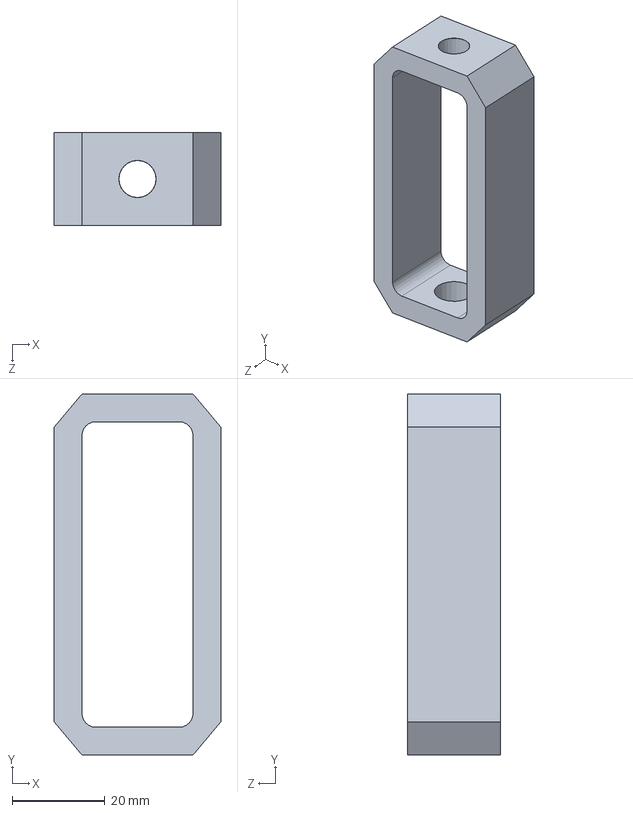
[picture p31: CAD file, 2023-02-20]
CAD SPIF-A/SPIF-A_v2 version2/Pecas Minhas/PerfilO_78.SLDPRT
36.0 x 78.0 x 20.0 mm

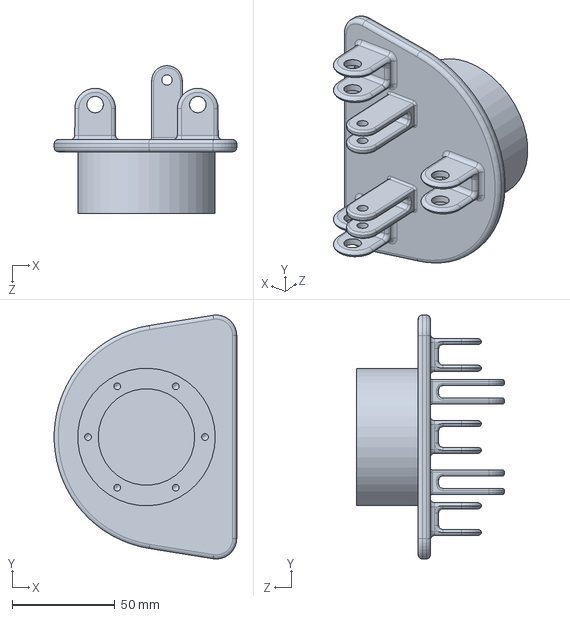
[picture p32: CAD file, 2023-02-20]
CAD SPIF-A/SPIF-A_v2 version2/Pecas Minhas/Base.SLDPRT
88.9 x 118.9 x 72.0 mm

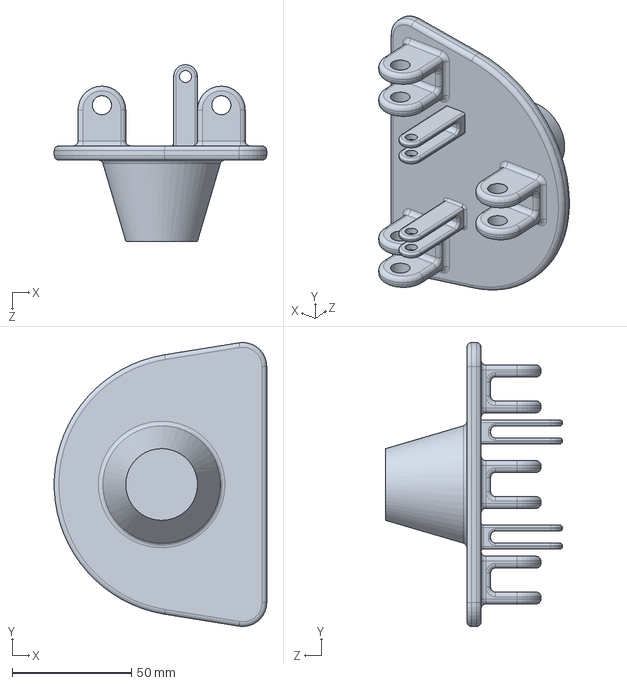
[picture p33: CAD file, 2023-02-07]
CAD SPIF-A/SPIF-A_v2 version1/componentes of mine/BaseRedonda.SLDPRT
88.9 x 118.9 x 74.0 mm

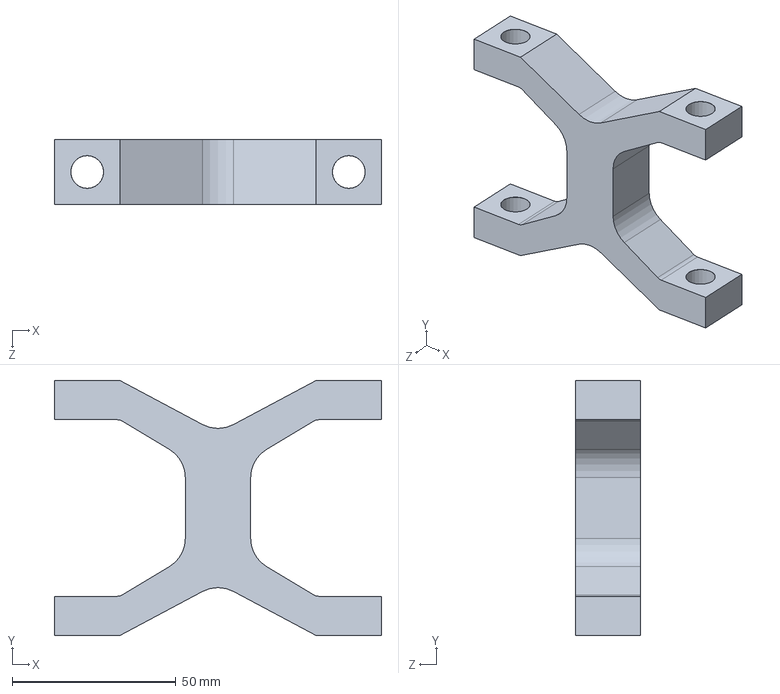
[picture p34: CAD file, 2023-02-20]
CAD SPIF-A/SPIF-A_v2 version2/Pecas Minhas/PerfilH_78.SLDPRT
100.0 x 78.0 x 20.0 mm

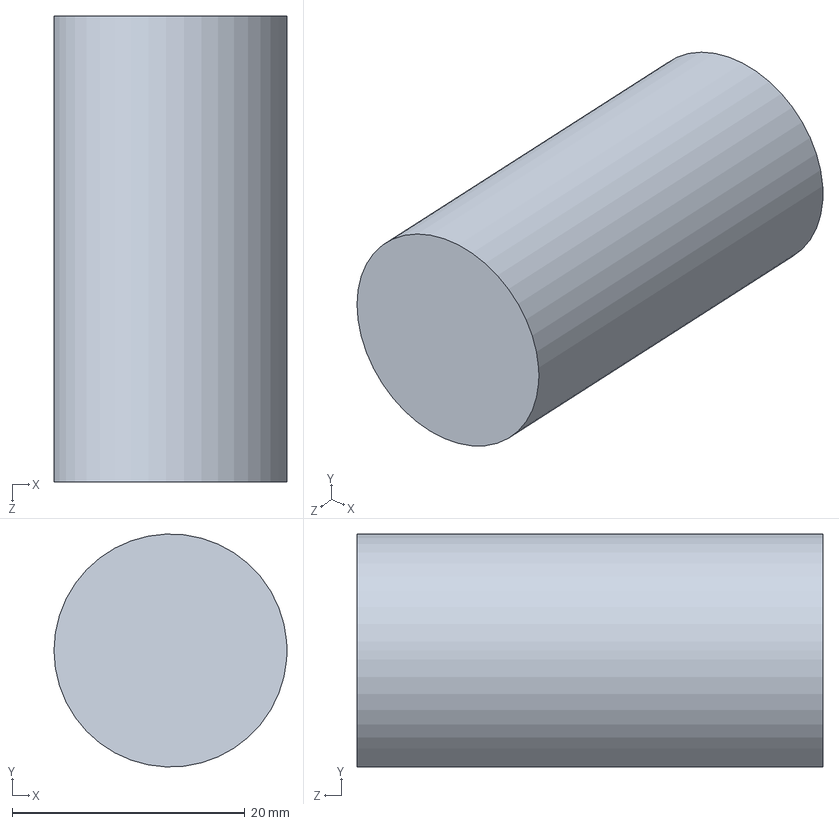
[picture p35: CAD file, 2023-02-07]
CAD SPIF-A/SPIF-A_v2 version1/componentes of mine/PerfilRedondo_20_80.SLDPRT
20.0 x 20.0 x 40.0 mm

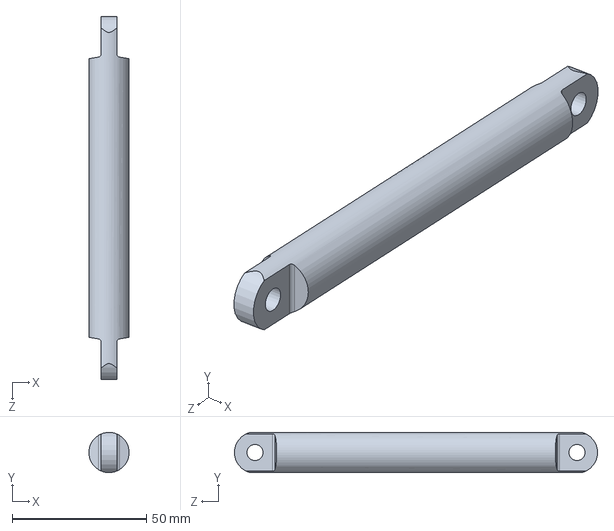
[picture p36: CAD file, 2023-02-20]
CAD SPIF-A/SPIF-A_v2 version2/Pecas Minhas/PerfilRedondo_10_100.SLDPRT
15.0 x 15.0 x 135.3 mm

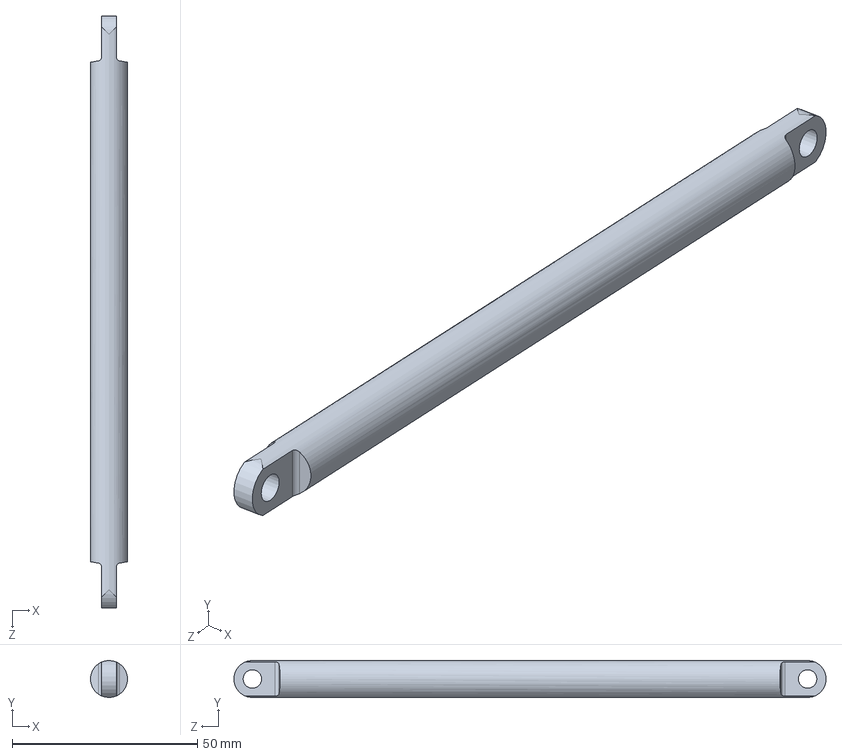
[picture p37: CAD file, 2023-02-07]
CAD SPIF-A/SPIF-A_v2 version1/componentes of mine/PerfilRedondo_10_150mm.SLDPRT
10.0 x 10.0 x 159.9 mm

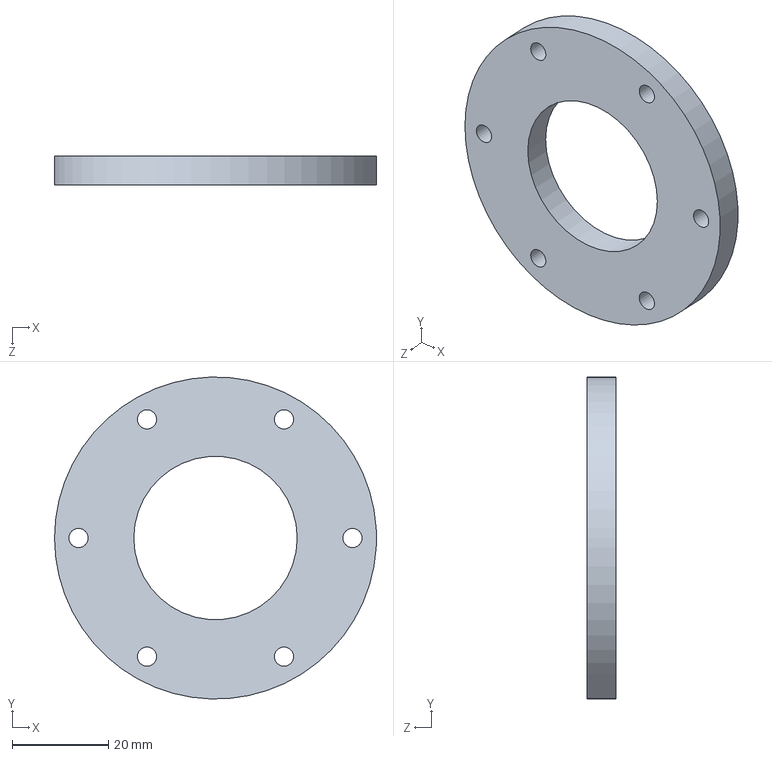
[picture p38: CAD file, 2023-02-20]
CAD SPIF-A/SPIF-A_v2 version2/Pecas Minhas/Tampa_Base.SLDPRT
67.0 x 67.0 x 6.00 mm

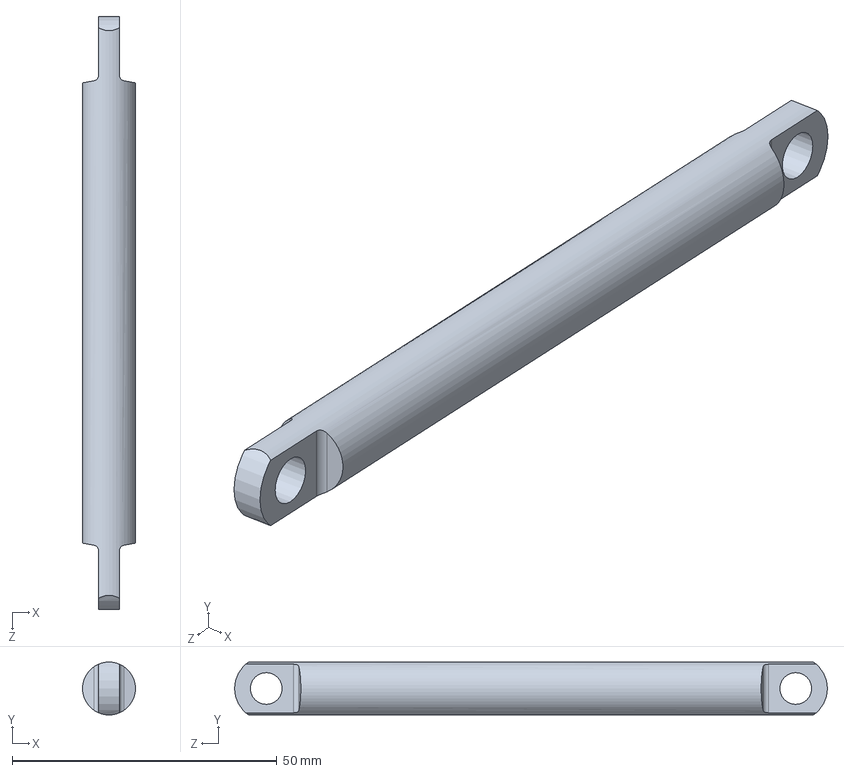
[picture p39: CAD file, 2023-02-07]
CAD SPIF-A/SPIF-A_v2 version1/componentes of mine/PerfilRedondo_10_100.SLDPRT
10.0 x 10.0 x 112.0 mm

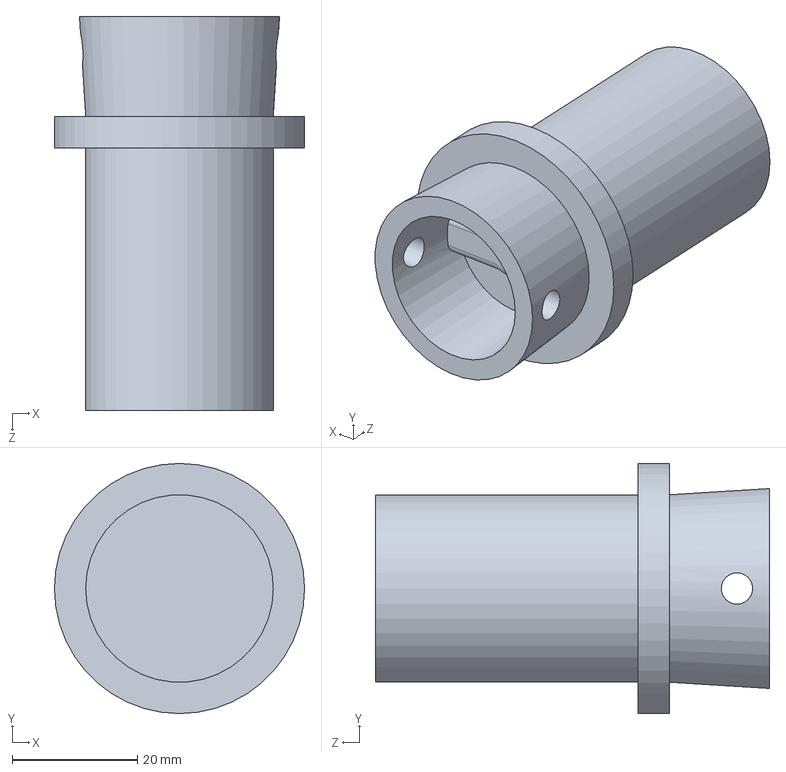
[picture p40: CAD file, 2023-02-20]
CAD SPIF-A/SPIF-A_v2 version2/Pecas Minhas/Veio_portaferramentas.SLDPRT
40.0 x 40.0 x 63.0 mm

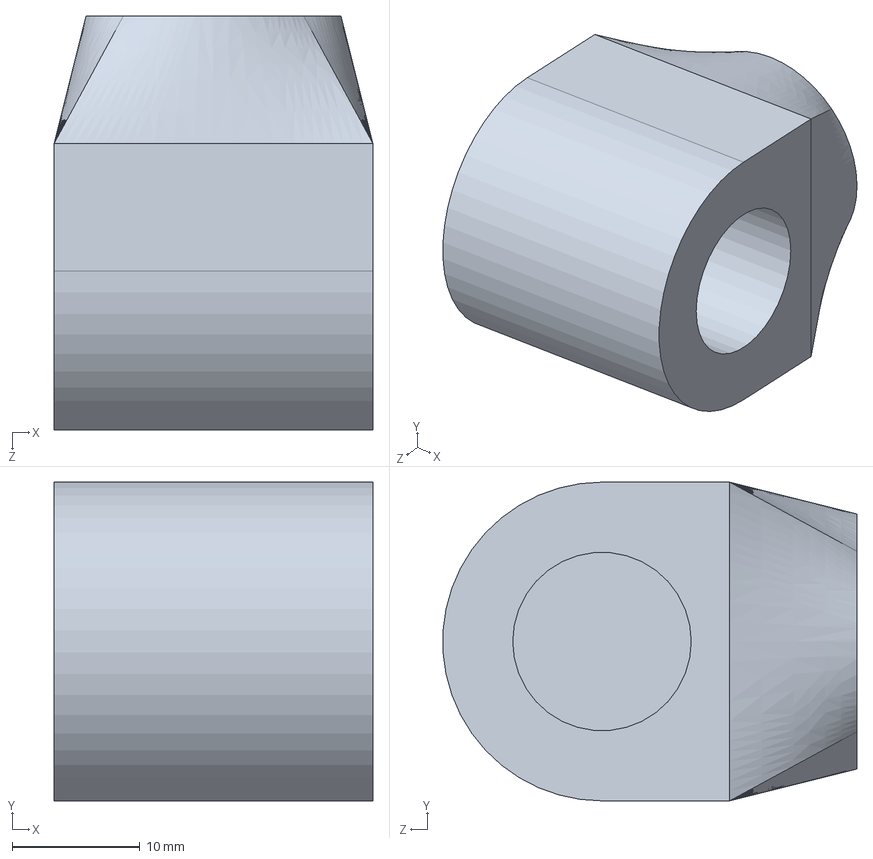
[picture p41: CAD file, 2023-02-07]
CAD SPIF-A/SPIF-A_v2 version1/componentes of mine/LigMotorBraco.SLDPRT
25.0 x 25.0 x 32.5 mm

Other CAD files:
CAD SPIF-A/SPIF-A_v2 version2/Pecas SKF/SKF_NKIB_5906.sldprt
CAD SPIF-A/SPIF-A_v2 version1/componentes of mine/LigBarraParalelograma.SLDPRT
CAD SPIF-A/SPIF-A_v2 version2/Pecas Minhas/LigMotorBraco.SLDPRT
CAD SPIF-A/SPIF-A_v2 version2/Pecas Minhas/PerfilO_40.SLDPRT
CAD SPIF-A/SPIF-A_v2 version1/componentes of Norelem/04250_082.sldprt
CAD SPIF-A/SPIF-A_v2 version1/componentes of Norelem/27620_1020_adapted.SLDPRT
CAD SPIF-A/SPIF-A_v2 version1/componentes of Norelem/27620_1020_fix.SLDPRT
CAD SPIF-A/SPIF-A_v2 version1/componentes of Norelem/27620_1020_fix_1.SLDPRT
CAD SPIF-A/SPIF-A_v2 version1/componentes of Norelem/27624_10_0812.sldprt
CAD SPIF-A/SPIF-A_v2 version1/componentes of Norelem/27624_10_1015.sldprt
CAD SPIF-A/SPIF-A_v2 version1/componentes of Norelem/27624_10_1015_adapted.SLDPRT
CAD SPIF-A/SPIF-A_v2 version2/Pecas Minhas/LigBarraParalelograma.SLDPRT
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

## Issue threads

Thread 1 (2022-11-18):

Study the best configurations _ Case 1

TatianaResend, 2022-11-18:
Case 1:
It is the most used, 2 arms in parallel (delta 2)

Case 1.1:
Distance between motors: 50 mm

Closed 2023-02-02.

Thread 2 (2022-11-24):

Study the best configurations _ Case 2

TatianaResend, 2022-11-24:
Case 2:
2 arms in parallel (delta 2), but on the first arm use the second redundancy (elbow up) and on the second arm the first redundancy (elbow down)

Case 2.1:
Distance between motors: 50 mm

Closed 2023-02-02.

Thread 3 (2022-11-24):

Study the best configurations _ Case 3

TatianaResend, 2022-11-24:
Case 3:
2 arms in series

Distance between motors: 50 mm

- L1 = 100;
- L2 = 150;
- y _ work area = -130 mm
- x_work area = same vertical as the first motor

Conclusion:
- Since the motors are places in series the error will accumulate and be greater than caso 1 #1 and case 2 #2.
- The maximum torque is higher than case 1. For case 2, from motor 1 is equal and from motor 2 the difference is not considerable. On the right side it is smaller but on the left side it is larger (component at x has a weight of 3x).

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

Closed 2023-02-02.

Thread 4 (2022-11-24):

Study the best configurations _ Case 4

TatianaResend, 2022-11-24:
[https://www.youtube.com/watch?v=6EtXycVGJg4&ab_channel=Rudmin](url)

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

[Explicação Case 4_PT.txt](https://github.com/TatianaResend/SPIFA-e-v2.0/files/10086485/Explicacao.Case.4_PT.txt)
They’re just two linkages attached with pins. The only design choices to make are the length of the arms, the angle of the pins, and the distance between the two tracks. You can adjust each of these to increase or decrease the range of motion for the end efector.

They’re actually surprisingly straightforward. Each of the carriage/arm assemblies has a fixed plane of motion, set by the fixed angle of the pin where the arm attaches. You just take the normal vector of that pin, plus the location along the track to get the equation for the three planes. Then you can actually just solve each of them independently, since they only depend on the location of the one specific carriage and the desired position of the end effector.

But how do you keep the system from oscillating from over correction?
Typically with a PID controller. Depending on the design requirements you’re trying to meet, you can tune the P, I, and D coefficients to change the behavior. To get rid of oscillation, you would bump up the D coefficient so the robot slows down as it approaches the target position.

The big benefit of the tripteron over the delta design is the linear control. That means no singularities to worry about, you have the same resolution and thrust characteristics everywhere in your work envelope and the forward and inverse kinematics are all trivial. It makes it very easy to work with. I was able to use a stock G-code interpreter and a spreadsheet to make the movements you see here.

Having fully orthogonal axes would have meant making a left and right hand version of each of the back carriage joints. By making those arms 90 degrees when projected onto the XY plane, those parts can be made identical and simply rotated 90 degrees from each other. It was just a little bit simpler to build that way.

Closed 2023-02-02.

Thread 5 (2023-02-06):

Simulations

TatianaResend, 2023-02-06:
Calculate the forces to which each of the connections is subjected.
Used safety factor 1.5
Material: "maraging" steel (used in aviation and molds)

TatianaResend, 2023-02-06:
Fast Iron - AISI: M2; DIN: 1.3343
Maraging steel - AISI: MIL-S-46850; DIN: WNr 1.6359
https://www.villaresmetals.com.br/villares/pt/Produtos/Ligas-Especiais/Acos-Maraging/VART250QA-MIL-S-46850

TatianaResend, 2023-02-06:
Create Motion Analysis:
- New Motion Study
- Upper left corner select option: Motion Analysis
- Assign the forces
- Assign the rotary motor
- Create a table motion

Possible errors:
- If after applying the RotaryMotor, the parts come loose, change the phase of rotation
- If number of new element states doesn't match number of old ones, try changing degree of rotation and recalculating

TatianaResend, 2023-02-07:
# Simulation in Motion Analysis
Create Simulation:
- Select in features the "Simulation"
- In Motion Analysis create a simulation
- Select the part to simulate and desired time interval
- Calculate the simulation

Possible errors:
- When trying to simulate several objects took too long and did not display the results correctly, then it is better to choose to crete new studies and simulate part by part

TatianaResend, 2023-02-13:
Motion Analysis - table task
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

TatianaResend, 2023-02-20:
Results:
- The upper connection piece on the right side (```27620_1020_adapted```) passes the yielding tension; therefore, it is necessary to check the simulation and probably change the piece to ```27620_1224``` and consequently the piece ```27624_10_1015``` to ```27624_10_1218```.
- The connections with the base can be changed from  ```27624_10_0812``` to ```27624_10_1015``` to be more uniform and increase the safety factor.
- It is necessary to change ```perfilRedondo_120```, changing it from being a single bar in the middle to two, as it obstructs movement.

TatianaResend, 2023-02-20:
To determinate the critical elements, one can start by constructing and analyzing a graph of the magnitude of the reaction force.

TatianaResend, 2023-03-10:
In the first approach, replace the part ```27620-1020``` with ```27624-05-1020```. I don't remember the difference on the 1st and 2nd try, but on the first one the maximum reaction force is 10592 N (similar to part ```27620-1020```).

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

 On the second attempt, the maximum reaction force is 5726 N. I probably got it wrong earlier, as the simulation currently looks correct.

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

Anyway, the moment caused in the sections is around 40MPa and 73MPa, which does not justify the passage of the yield stress.

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

Doubt:
- as the machine is symmetric, shouldn't the von Mises stresses be symmetric too?

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

https://user-images.githubusercontent.com/101273005/224268837-03615d00-7d6f-438f-99ae-26f39841b55d.mp4

TatianaResend, 2023-04-20:
# Simulate the structure
To simulate the structure, static simulation was used.

I started by simulating the structure with 30x30mm profiles and I had a safety factor of 0.2 so I increased it to a 45x45mm profile and placed some diagonal profiles passing to a safety factor greater than 1.3

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

TatianaResend, 2023-05-01:
Final simulation results: [simulacoes.pdf](https://github.com/TatianaResend/SPIF-A_v2/files/11367120/simulacoes.pdf)

TatianaResend, 2023-05-01:
I still need to finish the written part, then I can close the issue

Closed 2023-05-18.

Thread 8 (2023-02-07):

Study of kinematics

TatianaResend, 2023-02-07:
- [x] Introduction
- [x] Architecture definition
- [x] Requirements for the machine

TatianaResend, 2023-02-07:
### Introduction:
The introduction talks about the hypotheses thought at the beginning:
- robotic arms (in parallel and/or series)
- spindle
- case 4 (#4 )

TatianaResend, 2023-03-25:
Before introduction about the architecture hypotheses, write the requirements for the machine.

TatianaResend, 2023-04-01:
It remains to review the last paragraph of the writing and then this issue can be closed.

Closed 2023-04-08.

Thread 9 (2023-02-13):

New config: Config_v4

TatianaResend, 2023-02-13:
### Notes:
- The force was verified on the pin of part "27620_1020", which was thought to be one of the critical points. It suffers a tension of around 40MPa (any steel resists).

### Changes:
- Normalize to 10 mm the maximum of components
- Change the shape of the large bars (PerfilRedondo_20)
- As purchased components (exc. "27624-10") must not be changed to obtain a greater working range, the inclination of the large bars can be changed.

TatianaResend, 2023-02-13:
### Toolholder:
Look for solutions like the HSK cone.
https://sanchesblanes.com.br/produtos/cones-hsk

TatianaResend, 2023-02-14:
Folder restructuring: Arm 1 divided between Primary arm and Secondary arm. And the primary in Rigid body 1.1 and Rigid body 1.2.
Arm 2 - assembly divided into Rigid body 2.1 and Rigid body 2.2.
Adding a new folder: Tool holder.

TatianaResend, 2023-02-14:
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

TatianaResend, 2023-02-20:
## Notes:
- In order to obtain a greater working range, it was not decided to change the inclination of the large bars as initially stated, it was decided to change the length of the upper arms from 100 mm to 120 mm.

Closed 2023-02-20.

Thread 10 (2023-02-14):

Toolholder

TatianaResend, 2023-02-14:
There are no toolholders on the market specially built for SPIF processes. Therefore, the toolholder will be chosen from an existing one for another process and will be adapted to the specific needs of incremental sheet metal forming.

TatianaResend, 2023-02-14:
Professors suggestion:
- Use an HSK type cone, which are for cutting tools with a cylindrical shank. Choose a cone that is tightened by a screw so that tool changes are simple. For this case, select the smallest cone.
- Chosen example: " HSK- A32 - Tool holder form B (WELDON)", for DIN 1835-B / DIN 6535 - HB
https://sanchesblanes.com.br/produto/hsk-a32-porta-ferramentas-forma-b-weldon

- Similar product, on another site offering CAD: https://www.haimer.biz/products/tool-holders/din-69893-hsk-a-hsk-e-hsk-f/hsk-a32/weldon-tool-holder.html

TatianaResend, 2023-02-14:
https://www.youtube.com/watch?v=rZldZqrHmCM

TatianaResend, 2023-02-14:
video of tool holder assembly with shaft:
https://youtu.be/ychhZYKZqdw?t=31

TatianaResend, 2023-02-14:
### Toolhoolder components:
 - Base
 - NKIB 5906: Combined angular contact ball/needle roller bearing for axial loads in both directions
 SKF: https://www.skf.com/pt/products/rolling-bearings/roller-bearings/needle-roller-bearings/combined-needle-roller-bearings/productid-NKIB%205906
- Transmission shaft
- Weldon tool holder HSK-A32
- Base cover

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

TatianaResend, 2023-02-14:
Relevant information on the choice of toolholder can be found in Sónia Marabuto's thesis.

TatianaResend, 2023-02-22:
The toolholder placed in the CAD was an internal diameter of 6, so it is preferable to change to the one with an internal diameter of 8.

TatianaResend, 2023-03-14:
I changed the toolholder to diameter 8.
Documentation for this task is missing.

TatianaResend, 2023-04-10:
I already wrote it, but it remains to put the images in the documentation.

Closed 2023-04-25.

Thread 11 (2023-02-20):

New config: Config_v5

TatianaResend, 2023-02-20:
## Changes:
- Add a bar at the top of the parallelogram, thus changing from a single bar in the middle to one on each side.
- Confirm that in my pieces the corners all have fillets.
- The upper connection piece on the right side ("27620_1020_adapted") change the piece to "27620_1224" and consequently the piece "27624_10_1015" to "27624_10_1218".
- The connections with the base can be changed from 27624_10_0812 to 27624_10_1015 to be more uniform and increase the safety factor.

## New:
- Study the machine's structure
- Add the motor, gearbox and transmission system.

TatianaResend, 2023-05-18:
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

Closed 2023-05-18.

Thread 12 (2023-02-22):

Motor + reducer position

TatianaResend, 2023-02-22:
To discover the best configuration of the motors in the machine, it is necessary to analyze several hypotheses and compare them.

TatianaResend, 2023-02-22:
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

TatianaResend, 2023-02-22:
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

TatianaResend, 2023-02-22:
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

TatianaResend, 2023-02-22:
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

TatianaResend, 2023-02-24:
## Notes:
- Try to find some information about efficiency (compare pallet reducers and worm reducers), to justify the choice without just being based on the volume of the assembly.
- The engines will be placed one on each side as it is not worth having them deviated, as it requires an additional transmission.
- Link from a reducer supplier:  https://www.tecnopower.es/

TatianaResend, 2023-02-24:
I think we need a torque of 665Nm and as the motors are 12Nm, you need a reducer, at least 56:1.

I looked on the TECNOPOWER website and found precision planetary reducers straight at 90º, that is to say they have an L configuration but either I don't know how to check their catalog or else to comply with the configurations the reducer is much bigger than what I was expecting . In this case, I was looking at this: https://www.tecnopower.es/producto/serie-afr and from the datasheet it seems to me that it would have to be the AFR180 model which is quite large.

As for straight gear reducers, it seems to me that there are none that meet the required output of 665Nm.

Regarding endless reducers I found this one: https://www.tecnopower.es/producto/eje-solido but from the datasheet I didn't find out which model will be needed.

So regarding the reducer, I'm not sure which is the best option or if there are other sites with other models.

TatianaResend, 2023-02-27:
### Ideally, a 90º planetary reducer will be used, as a good configuration is achieved and, compared to worn reducers, they are more efficient.

### AHK140_24:
- It was confirmed that the AHK140_24 reducer could be a good candidate. For 2 steps, a reduction of 55 and torque of 805 Nm is achieved. With 3 stages, a reduction of 54 Nm and torque of 845 Nm.
- As the efficiency of the reducer is higher with 2 steps compared to 3 steps, a reduction of 55 would be preferable.
- But, this reducer belongs to the upper class, that is, it has a high price.

https://www.tecnopower.es/producto/serie-ahk-2-etapas

### ABR142:
- A more economical solution will be an AB series gearbox.
- Preferably an ABR as it has a 90º configuration which makes it the most compact overall configuration.
- Namely, ABR142, which achieves a reduction of 60 with a torque of 600 Nm. Despite the torque being less than the required 665 Nm, the maximum torque is 1080 Nm which is more than enough.
- The maximum torque point is reached at the upper extreme points, that is, it will only be reached in specific cases and not in continuous work.
- It remains to confirm the dimensions and compatibility of this reducer as well as obtain its CAD, for this the datasheets must be carefully checked and, if necessary, contact the supplier.

http://www.apexdyna.com/download/catalog/ABABR-Eng.pdf
http://www.apexdyna.com/ABR_pro.aspx#Object_PDF.aspx?ProductNo=ABR001&Item=Specification&Lan=E
https://www.tecnopower.es/producto/serie-abr

TatianaResend, 2023-03-27:
The reducer is secured to the frame at the top.
In order to ensure that it is secure, it can also be fixed in the connection area between the reducer and the motor.
This part will be drawn later because I don't have the CAD of the component that connects the reducer to the motor.

TatianaResend, 2023-05-18:
I won't be implementing the reducer in the prototype as I don't have the available funds to purchase them and/or the time to implement them in the prototype.

Closed 2023-05-18.

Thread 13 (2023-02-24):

Table: axis x

TatianaResend, 2023-02-24:
Regarding the X axis, you can opt for a linear axis solution with a worm or for a rotary axis and work with polar coordinates.
- If it is a linear axis in X, although the machine must be wider, the minimum width is 500mm, it is still not enough to accumulate the YZ engines horizontally without increasing the width of the machine.
- If the shaft is rotary, with a vertical shaft, probably the solution with vertical motors can be more compact.

TatianaResend, 2023-02-24:
Link youtube axis-x: https://www.youtube.com/watch?v=I4PshKtwpqs

TatianaResend, 2023-02-26:
To use a spindle of this type, the motor needs to be “in front” of the spindle, which makes the system less compact. To put the motor in the opposite position, a transmission system would be needed, but I don't see how it could be fixed to the structure efficiently.

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

TatianaResend, 2023-02-26:
Types linear motion control:
- ball-screw drives
-  lead-screw drives
- belt drives

Additional specification when considering linear motion control design:
- force
- speed
- travel distance
- accuracy
- repeatability
- lifetime requirements or the duty cycle

### Notes:
- Ball screw generally have lower speed than belt drives
- Ball screw actuators use ball bearings and are more expensive but provice less friction compared with lead-screw actuators
- Ball screw linear motion drives have relatively high thrust capacity
- Ball screw drive combine repeatable motion and stiff system that handles high forces and moments. Such systems work well in precision-positioning applications with high loads and high duty cycles.

Belt drives vs Ball-screw:
- Belt drives are quiet and good for high-throughput, lower-precision applications.
- More-expensive ball-screw drives provide high efficiency, accuracy, and stiffness.

https://www.youtube.com/watch?v=WrFy2objT5k

TatianaResend, 2023-02-26:
polias norelem: https://norelem.es/pt/Vis%C3%A3o-geral-de-produtos/Sistemas-e-componentes-para-a-constru%C3%A7%C3%A3o-de-m%C3%A1quinas-e-equipamentos/22000/Correias-dentadas-Polias-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
festo; https://www.festo.com/pt/pt/p/atuador-linear-do-parafuso-de-bolas-id_ELGC_BS/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

TatianaResend, 2023-03-10:
To control the movement of linear actuators, I have two approaches:
- One motor for each linear actuator: simple in terms of mechanical design, more complicated in terms of automation design because it is more complicated to synchronize both actuators and more expensive because it uses two motors
- One motor for the two linear actuators: a little more complicated in terms of mechanical design, simpler in terms of automation design and cheaper

TatianaResend, 2023-03-14:
## Calculations for validating the use of belt:
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

TatianaResend, 2023-03-27:
Understand the advantages and disadvantages of using one or two motors, taking into account that initially it is intended to use two motors.

The decision depends on whether to use the motor with the brake on the Z axis.

TatianaResend, 2023-04-01:
I found this solution for the actuator attachment:
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

So I asked for the quote for the electric actuator and I saw that the actuator on the "Unimotion" is expensive (996.84€), so I'll try to find out the price of the actuators on the "FESTO" website.

Now I'm waiting for FESTO's response to the profile update request to get the prices.

TatianaResend, 2023-05-18:
:exclamation: :exclamation: :exclamation: Although I used the MTJ40 ECO L in the CAD, I believe it would be preferable to use the MTV40 1205, even though an additional piece is required to redirect the linear actuator's shaft.

Closed 2023-05-18.

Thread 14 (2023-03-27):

Mechanical Design – missing details

TatianaResend, 2023-03-27:
- [x] The reducer can also be fixed in the connection area between the reducer and the motor. #12
- [x] Confirm that the ```27620-1020``` component supports the stress. #5
- [x] Simulate the structure. #5
- [x] X-axis: decide whether one or two motors. #13
- [x] Fixing the table and the linear actuator. #13

TatianaResend, 2023-05-18:
I've done the missing details

Closed 2023-05-18.

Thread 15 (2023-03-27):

Test the motors

TatianaResend, 2023-03-27:
Make the necessary connections to plug in a motor and create C++ code to test the motors. Initially, you can test motor by motor individually.
The controller to be used initially will be an Arduino UNO but in the final project it will be a Controllino MEGA.

Using the AccelStepper library.

TatianaResend, 2023-04-03:
The first motor work.
I can rotate the angle I want through the accelstepper library.
Missing: try if the other motors also work

TatianaResend, 2023-04-13:
I already have the power supply part for the motors.
Just missing wires to be able to connect and test.

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

TatianaResend, 2023-05-18:
All engines individually work correctly

Closed 2023-05-18.

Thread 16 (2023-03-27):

Calculate the inverse kinematics

TatianaResend, 2023-03-27:
The equations of the direct and inverse kinematics calculated initially do not represent a delta 2 robot, since initially a planar RR robot was thought (while a delta 2 robot consists of two arms of the planar RR type).
It is necessary to calculate the equations of the direct and inverse kinematics of the delta 2 robot.

TatianaResend, 2023-03-28:
I found this [article](https://www.researchgate.net/publication/321771824_D2_Delta_Robot_Structural_Design_and_Kinematics_Analysis) that demonstrates the equations for direct and inverse kinematics, but the axes are different than what I want.

TatianaResend, 2023-03-28:
In order to facilitate the kinematics, I can place the zero of the Z axis aligned with the motors.
If you want to give the coordinates such as (0,0,0) to be the center point of the machine on the table plane, just make the z coordinate be (z+constant) where the constant is the distance from the motors line to the table.

TatianaResend, 2023-03-28:
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

Closed 2023-04-08.

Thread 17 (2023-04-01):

Controller

TatianaResend, 2023-04-01:
For motor control, a ```controllino MEGA``` is being considered.

### I/o digital list:
- Qty. 1 - INPUT - Emergency button
- Qty. 1 - INPUT - Barrier signal
- Qty.1 - INPUT - Reset button
- Qty. 3 - INPUT - Home switch
- Qty. 3 - INPUT - Drives alarm
- Qty. 3 - INPUT - End of course
- Qty. 3 - OUTPUT - Drives Step
- Qty. 3 - OUTPUT - Drives direction
- Qty. 1 - OUTPUT - Drives enable

So, I need 12 inputs and 7 outputs. A total of 19 i/o digital.

### Controlino
- The [Controlino Maxi ](https://www.controllino.com/product/controllino-maxi/) exactly the expected number of inputs, which is not a good practice because in the future you might want to control something else.
- The [Controllinno Maxi automation](https://www.controllino.com/product/controllino-maxi-automation/) has one more output than expected, but once again having only one reserve output is not enough.
- The [Controllinno MEGA](https://www.controllino.com/product/controllino-mega/) has enough inputs/outputs and the price ratio when compared with the Controllino MAXI is advantageous.

TatianaResend, 2023-05-18:
Code development and testing are being done using an Arduino UNO.

Closed 2023-05-18.

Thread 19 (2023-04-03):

Add the second YZ axis motor and synchronize the motors

TatianaResend, 2023-04-03:
Add the second YZ axis motor:
- [x] Understand how the power supply will work
- [x] Try to get wires for the necessary connections
- [x] Synchronize the motors

TatianaResend, 2023-05-18:
By using the ```multistepper.h``` library the engines work in a synchronized way,

Closed 2023-05-18.

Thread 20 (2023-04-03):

Sending commands from the computer

TatianaResend, 2023-04-03:
Create an application to receive computer commands
I can start by looking at the application made by [Jorge Fernandes](https://github.com/JorgeFernandes-Git/ISFM/tree/main/GUI_ISFM_VisualBasic) and adapt it to what I need. Before that, it's important to understand how to make apps with VisualBasic.

TatianaResend, 2023-04-14:
Try to use what was done in SPIF-A
First I need to understand how the interface is and how to receive data and then adapt the new SPIF-A

TatianaResend, 2023-04-20:
Now I can send some commands to the arduino.

## Process of sending coordinates:
### In MATLAB:
- loading and reading the file with the G code
- transformation of G code into x,y,z coordinates
- transformation of coordinates into angles (inverse kinematics) - saving the sequence of angles in a txt file

### In Arduino:
- Reads the txt file with the sequence of angles
- Commands the motors to execute the movement

TatianaResend, 2023-05-18:
At this moment, I need to buy the SD card reader to be able to implement

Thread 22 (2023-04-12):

Receive the encoder signal and measure the positioning error

TatianaResend, 2023-04-12:
- [ ] Receive the encoder signal
- [ ] Measure the positioning error

TatianaResend, 2023-04-12:
I'm still not sure, but I don't think I can read the pulses in real time with code and calculate the positioning error.
If I want to see the positioning error, I can see it in the Drive Software “Launch STEPPERONLINE”.

As it is in a closed loop, theoretically it will receive feedback and run accordingly if the PID values are correct.
But I need to confirm this.

TatianaResend, 2023-04-12:
Graphic in Drive Software with SpeedProfile and SpeedFeedback:
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

Graphic in Drive Software with PositionProfile and PositionFeedback:
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

TatianaResend, 2023-04-12:
A closed-loop stepper drive is a type of stepper motor driver that incorporates a feedback mechanism to improve the performance and accuracy of the stepper motor.

In a traditional open-loop stepper motor system, the motor rotates a certain number of steps in response to each command signal from the controller, but there is no feedback mechanism to confirm that the motor has actually moved that precise number of steps. This can lead to errors, especially when the load on the motor changes or when the motor is operating at high speeds.

A closed-loop stepper drive system, on the other hand, uses a feedback sensor to measure the actual position of the motor shaft and provide this information back to the driver. The driver can then adjust the number of steps sent to the motor to ensure that it reaches the desired position accurately. This closed-loop control helps to compensate for any errors that may occur and improve the overall performance and accuracy of the stepper motor system.

Closed-loop stepper drives are commonly used in applications that require high precision and accuracy, such as in CNC machines, robotics, and medical equipment.

TatianaResend, 2023-04-12:
In the future, if there is an error in the positioning, I have to study the PID parameters

TatianaResend, 2023-06-21:
The motor is not showing power, so see the encoder parameters.
 - [ ] Test auto tuning

TatianaResend, 2023-08-03:
In principle the encoder is working correctly but the PID parameters can be improved.

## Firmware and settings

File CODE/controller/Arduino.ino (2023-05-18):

/*
 * This code was developed by Walid Khaled - Nile University graduating student 2021 
 * It is used to run 6DOF Manipulator with gripper attached.
 * You could run from Arduino Serial Monitor; just type the angles and coordinated time e.. -90 0 90 10 20 30 5
 * Also, it could be run from MATLAB e.. [-90 0 90 10 20 30 5], [-90, 0, 90, 10, 20, 30, 5]
*/

//////////////////////////////////////////////////////////////////////////////////////////////////////////////////////////////////////////////////////////////////////////////////////////////

#include <MultiStepper.h>
#include <AccelStepper.h>

// Definition of pins
// Pul & Dir
#define Pul_YZ1 2 
#define Dir_YZ1 3
#define Pul_YZ2 4 
#define Dir_YZ2 5

// Enable
#define Ena_YZ1 6
#define Ena_YZ2 7

// Pend & Alarm
#define Pend_YZ1 8
#define Alarm_YZ1 9
#define Pend_YZ2 10
#define Alarm_YZ2 11

//Stepper Motors Pin Configuration
AccelStepper motor_YZ1 (AccelStepper::DRIVER, Pul_YZ1, Dir_YZ1);     //PULSE Pin, Direction Pin , Stepper 1
AccelStepper motor_YZ2 (AccelStepper::DRIVER, Pul_YZ2, Dir_YZ2);     //PULSE Pin, Direction Pin , Stepper 2

// Create at instance of MultiStepper to coordinate the motors
MultiStepper multiStepper; // upt to 10 steppers we can use MultiStepper

//Driver Mode
int DPulsePerRev[] = {400, 400}; //MicroStepping mode 400 is half-step, 800 is quarter-step
int PulPerRev = 400;

//Set Positions for Motors
long positions[2]; //Array of desired stepper positions
long prev_positions[2]; //Array of previous stepper positions

//Set Speeds for Motors
float n = 120;
float MotorSpeeds[] = {((n/60)*DPulsePerRev[0]), ((n/60)*DPulsePerRev[1])};
float TimeTaken;
float Actual_MotorSpeeds[2];
float Actual_n_RPM[2];

//Set Limit Switches 
//long LSwitchS[6];
//int Lswitch1 = 14;
//int Lswitch2 = 15;
//int Lswitch3 = 16;
//int Lswitch4 = 17;
//int Lswitch5 = 18;
//int Lswitch6 = 19;

//Set Inputs 
String MATLABdata;
char *arr_char_strings[3];
char *ptr = NULL;
byte index;
String arr_strings[3];
float arr_input[3];

//Set Gripper
//#include <Servo.h>
//Servo myservo;  
int pos = 0;    

// variables
int vel = 1500;
//////////////////////////////////////////////////////////////////////////////////////////////////////////////////////////////////////////////////////////////////////////////////////////////

void setup() {
  Serial.begin(9600);
  Serial.setTimeout(10);

  // Set the inicial speeds of the motors
  motor_YZ1.setSpeed(vel); 
  motor_YZ2.setSpeed(vel); 
  
  //Add the motors to the Multistepper instance
  multiStepper.addStepper(motor_YZ1);
  multiStepper.addStepper(motor_YZ2);

  //myservo.attach(A6); 
  
  pinMode(Pul_YZ1, OUTPUT);
  pinMode(Pul_YZ2, OUTPUT);
  pinMode(Dir_YZ1, OUTPUT);
  pinMode(Dir_YZ2, OUTPUT);
  
  pinMode(Ena_YZ1, OUTPUT);
  pinMode(Ena_YZ2, OUTPUT);
  
  pinMode(Pend_YZ1, INPUT);
  pinMode(Pend_YZ2, INPUT);
  pinMode(Alarm_YZ1, INPUT);
  pinMode(Alarm_YZ2, INPUT);
  
  digitalWrite(Ena_YZ1, LOW);
  digitalWrite(Ena_YZ2, LOW);
  
  
}

//////////////////////////////////////////////////////////////////////////////////////////////////////////////////////////////////////////////////////////////////////////////////////////////

void loop() {
  if (Serial.available() > 0){
    MATLABdata=Serial.readString();                      // read data as string.
    //Serial.println("Data Received");
    
    if (MATLABdata == "1"){
      //Serial.println("Homing ....");
      homing();
    }
    
    else if (MATLABdata == "2"){
      //Serial.println("Zero Postions ....");
      automatic();
    }
    
    else if (MATLABdata == "3"){
      Serial.println("Homing ....");
      homing();
    }

    else if (MATLABdata == "4"){
      Serial.println("CG End Position");
      zeros();
    }

    else if (MATLABdata == "5"){
      Serial.println("Gripper Open");
      open_gripper();
    }

    else if (MATLABdata == "6"){
      Serial.println("Gripper Close");
      close_gripper();
    }

    else{
      char buf[MATLABdata.length()+1];                   // length (with one extra character for the null terminator, a null character (ASCII code 0) to tell where the end of a string is).
      MATLABdata.toCharArray(buf,MATLABdata.length()+1); // Copy it over in buffer, sizeof (buf) = MATLABdata.length()+1.
  
      index = 0;                                         // define index.
      ptr = strtok(buf, " ");                            // tokenizing of a string using the strtok() function that returns a variable of type char separated based on a delimiter (" ").
      while(ptr != NULL){                                // iterate the list until it is empty.
        arr_char_strings[index] = ptr;                   // append in array of type char.
        //Serial.print("arr_char_strings: ");
        //Serial.println(ptr);
        index++;                                         // increment index by 1.
        ptr = strtok(NULL, " ");                         // takes a list of delimiters.
      }
      
      
      for (int r = 0; r < index; r++){
        arr_strings[r]=String(arr_char_strings[r]);      // convert from char to string type.
        arr_input[r]=arr_strings[r].toFloat();           // convert from string to float type.
      }

   
      moving();                                          // calling moving function (RUN).
      //Serial.println("moving");
    }                                           
  }    
}

//////////////////////////////////////////////////////////////////////////////////////////////////////////////////////////////////////////////////////////////////////////////////////////////

void calibration() {
  Serial.println("Calibration");
}

//////////////////////////////////////////////////////////////////////////////////////////////////////////////////////////////////////////////////////////////////////////////////////////////

void zeros() {
  Serial.println("zeros");
  //int angle1 = 45;
  //axis1.move(angle1);
  //axis1.runToPosition();
}

//////////////////////////////////////////////////////////////////////////////////////////////////////////////////////////////////////////////////////////////////////////////////////////////

void homing() {
  Serial.println("Homing"); 
}

//////////////////////////////////////////////////////////////////////////////////////////////////////////////////////////////////////////////////////////////////////////////////////////////

void automatic() {
  Serial.println("automaic");
  // open the file
  //ifstream input(filename);
  
}

//////////////////////////////////////////////////////////////////////////////////////////////////////////////////////////////////////////////////////////////////////////////////////////////

void moving() {
  int angle1 = arr_input[0];
  int angle2 = arr_input[1];

 Serial.print("moving- angle1:");
 Serial.print(angle1);
 Serial.print(" angle2:");
 Serial.println(angle2);
 
 // Create an array of positions for the motors
 long positions[] = {angle1, angle2};
 //long positions[] = {90, 90};

 // Move the motors to the desired positions in a coordinated fashion
 multiStepper.moveTo(positions);

 // Execute the movements
 while (multiStepper.run()) {
    // Nothing to do here, just wait until the motors reach the desired positions
 }

   //motor_YZ1.move(angle1);
   //motor_YZ1.runToPosition();
 //  multiStepper.moveTo(positions);
 //  multiStepper.run();
}

//////////////////////////////////////////////////////////////////////////////////////////////////////////////////////////////////////////////////////////////////////////////////////////////

void close_gripper() {
  Serial.println("close_gripper");
}

//////////////////////////////////////////////////////////////////////////////////////////////////////////////////////////////////////////////////////////////////////////////////////////////

void open_gripper() {
  Serial.println("open_gripper");
}

//////////////////////////////////////////////////////////////////////////////////////////////////////////////////////////////////////////////////////////////////////////////////////////////

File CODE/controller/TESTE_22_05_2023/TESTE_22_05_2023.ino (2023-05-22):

#include <MultiStepper.h>
#include <AccelStepper.h>

// Definition of pins
// Pul & Dir
#define Pul_YZ1 2
#define Dir_YZ1 3
#define Pul_YZ2 4
#define Dir_YZ2 5

// Enable
#define Ena_YZ1 6
#define Ena_YZ2 7

// Pend & Alarm
#define Pend_YZ1 8
#define Alarm_YZ1 9
#define Pend_YZ2 10
#define Alarm_YZ2 11

//Stepper Motors Pin Configuration
AccelStepper motor_YZ1 (AccelStepper::DRIVER, Pul_YZ1, Dir_YZ1);     //PULSE Pin, Direction Pin , Stepper 1
AccelStepper motor_YZ2 (AccelStepper::DRIVER, Pul_YZ2, Dir_YZ2);     //PULSE Pin, Direction Pin , Stepper 2

// Create at instance of MultiStepper to coordinate the motors
MultiStepper YZaxis; // upt to 10 steppers we can use MultiStepper

//Driver Mode: like all drives, just a common variable for all
int PulPerRev = 400;
float ConvPul = 1.11; // PulPerRev/360;

//Set Positions for Motors
long positions[2]; //Array of desired stepper positions
long prev_positions[2]; //Array of previous stepper positions

//Set Speeds for Motors
int MAX_SPEED = 1000;
int ACCELERATION = 500;

//Set Inputs
String MATLABdata;
char *arr_char_strings[3];
char *ptr = NULL;
byte index;
String arr_strings[3];
float arr_input[3];

//start functions
void CinInv(long coordY_CI, long coordZ_CI);
void homing();
void automatic();
void moving();

int angle1 = 0;
int angle2 = 0;

void setup() {
  Serial.begin(9600);
  Serial.setTimeout(10);

  pinMode(Pul_YZ1, OUTPUT);
  pinMode(Pul_YZ2, OUTPUT);
  pinMode(Dir_YZ1, OUTPUT);
  pinMode(Dir_YZ2, OUTPUT);

  // Initialize enable pin of the drivers as output
  pinMode(Ena_YZ1, OUTPUT);
  pinMode(Ena_YZ2, OUTPUT);
  digitalWrite(Ena_YZ1, LOW); // Start with motors enabled
  digitalWrite(Ena_YZ2, LOW); // Start with motors enabled

  // Set the inicial speeds and acceleration of the motors
  motor_YZ1.setMaxSpeed(MAX_SPEED);
  motor_YZ1.setAcceleration(ACCELERATION);
  motor_YZ2.setMaxSpeed(MAX_SPEED);
  motor_YZ2.setAcceleration(ACCELERATION);

  //Add the motors to the Multistepper instance
  YZaxis.addStepper(motor_YZ1);
  YZaxis.addStepper(motor_YZ2);

}


void loop() {

    if (Serial.available() > 0){
     MATLABdata=Serial.readString();                      // read data as string.

     if (MATLABdata == "1"){
       homing();
     }

     else if (MATLABdata == "2"){
       automatic();
     }

     else{
       char buf[MATLABdata.length()+1];                   // length (with one extra character for the null terminator, a null character (ASCII code 0) to tell where the end of a string is).
       MATLABdata.toCharArray(buf,MATLABdata.length()+1); // Copy it over in buffer, sizeof (buf) = MATLABdata.length()+1.

       index = 0;                                         // define index.
       ptr = strtok(buf, " ");                            // tokenizing of a string using the strtok() function that returns a variable of type char separated based on a delimiter (" ").
       while(ptr != NULL){                                // iterate the list until it is empty.
         arr_char_strings[index] = ptr;                   // append in array of type char.
         //Serial.print("arr_char_strings: ");
         //Serial.println(ptr);
         index++;                                         // increment index by 1.
         ptr = strtok(NULL, " ");                         // takes a list of delimiters.
       }

       for (int r = 0; r < index; r++){
         arr_strings[r]=String(arr_char_strings[r]);      // convert from char to string type.
         arr_input[r]=arr_strings[r].toFloat();           // convert from string to float type.
       }

       moving();                                          // calling moving function (RUN).
    }
  }
}


// ################################################################################################################################################################
// Function Homing
// ################################################################################################################################################################
void homing() {
  Serial.println("Homing");
}

// ################################################################################################################################################################
// Function Automatic
// ################################################################################################################################################################
void automatic() {
  Serial.println("automaic");
  // open the file
  //ifstream input(filename);
}

// ################################################################################################################################################################
// Function Moving
// ################################################################################################################################################################
void moving() {
  int coordX = arr_input[0];
  int coordY = arr_input[1];
  int coordZ = arr_input[2];
  // int coordX = 10;
  // int coordY = -73;
  // int coordZ = 250;

  static int realPosY = 0;
  static int realPosZ = 150;
  double alphaRAD = 0.00;
  double dist = 0.00;
  int inc = 0;
  double DeltaS = 5;
  long PrevPosY;
  long PrevPosZ;

  float yy = coordY - realPosY; //YF - Y0
  float zz = coordZ - realPosZ; //ZF - Z0

  if (yy != 0 || zz != 0) {
    dist = sqrt((pow(coordY - realPosY, 2)) + (pow(coordZ - realPosZ, 2))); //length of displacement vector
    //Change angle according to forward or retreat
    if (coordY > realPosY) {
      alphaRAD = atan((zz) / (yy)); //displacement vector angle
    } else {
      alphaRAD = atan((zz) / (yy)) + PI; //displacement vector angle + PI
    }

    inc = round(dist / DeltaS);

    for (int i = 0; i <= (inc); i++) {
      if (i < inc) {
        PrevPosY =  realPosY + (i * DeltaS * cos(alphaRAD)); //New position Y
        PrevPosZ =  realPosZ + (i * DeltaS * sin(alphaRAD)); //New position Z
      } else {
        PrevPosY = coordY;
        PrevPosZ = coordZ;
      }
      
      CinInv(PrevPosY, PrevPosZ);

      // Create an array of positions for the motors
      //long positions[] = {angle1, angle2};
      //long positions[] = {90, 90};
      
      // Move the motors to the desired positions in a coordinated fashion
      //multiStepper.moveTo(positions);
      motor_YZ1.moveTo(angle1);


      // Wait until the stepper motor has reached the position
      while (motor_YZ1.distanceToGo() != 0) {
        motor_YZ1.runSpeedToPosition();
      }
      // Execute the movements
      //while (multiStepper.run()) {
      // Nothing to do here, just wait until the motors reach the desired positions
      //}
    }
    realPosY = coordY;
    realPosZ = coordZ;
  }
}
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

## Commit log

2022-11-22 Create el
2023-02-07 Configuration with selected components
    [04250_082.sldprt, 04250_10.sldprt, 27620_1020_adapted.SLDPRT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]
2023-04-15 Make the app and communication with arduino
2023-05-22 Forward kinematics works. #18 Trajectory works. #23 Receiving information from the app works. #20
2023-06-05 organization of folders
    [3D-model_A_00903.SLDASM, 3D-model_A_00903.SLDPRT, 3D-model_A_00903.stp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]

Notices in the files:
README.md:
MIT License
